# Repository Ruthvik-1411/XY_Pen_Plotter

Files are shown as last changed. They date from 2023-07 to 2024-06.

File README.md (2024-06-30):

# XY_Pen_Plotter
<p align="center">
  
</p>
<p>The pen plotter is a drawing machine capable of creating complex designs, patterns, and artworks on paper or flat surfaces. It a type of CNC (Computer Numerical Control) machine designed to draw or sketch images using a pen or similar writing instrument. It operates on two or more axes, allowing precise control over the movement of the pen across the drawing surface. The pen plotter can execute complex patterns and designs with exceptional accuracy, making it an excellent tool for both artistic and technical applications.This repository contains all the information and resources you need to build your very own pen plotter.</p>

### Key Features
* <b>Low cost:</b> The structure of the pen plotter is made mostly out of wooden blocks and connected using available screws. The base for linear movement is achieved using linear rods that are extracted from a mini drafter. The electronic part of the plotter also uses 28byj-48 steppers which are the cheapest steppers. Most of the components of the plotter are just things lying around in the house.
* <b>Single Stepper Motor for X-Axis Movement:</b> The X-axis movement is managed by a 28byj-48 unipolar stepper motor, providing precise control over the horizontal positioning of the pen.
* <b>Two Stepper Motors for Y-Axis Movement:</b> The pen plotter features two stepper motors that work in parallel to control the movement of the pen along the Y-axis. This enables smooth and synchronized motion for creating detailed drawings.
* <b>GT2 Timing Belts for Enhanced Performance:</b> The plotter uses GT2 timing belts, known for their reliability and reduced backlash, ensuring consistent and accurate drawings.
* <b>Customizable Software Control:</b> The pen plotter is compatible with popular CNC software like GRBL (G-code sender) and can be easily controlled through a computer interface.

## Tools and Materials
* Wooden blocks (54x7 - 2, 40x7 - 2) any size to make a |=| structure.
* Smooth linear rods (from mini drafter) - 6 (2 along x, 4 along y in parallel)
* Rollers or linear bearings that allow for linear motion on rods.
* screws and other misc components for mechanical support
* 28byj-48 uniploar steppers - 3
* ULN2003 stepper motor driver - 3
* GT2 timing belt 1 mtr - 3
* 16 teeth 5mm bore timing pulley - 6(3 at motor shaft, 3 at other end)
* SG90 servo motor
* Limit switches - 3
* Arduino Uno R3 and jumper wires
* Capacitor 100nF (104) - 2
* Resistor 4.7K&#8486; (4k7) - 2
* Prototype board or breadboard
* USB cable and adapter (5V, ~1A) 
* Drilling tool would be handy
* Marker or pen and paper

## Hardware specifications and assembly
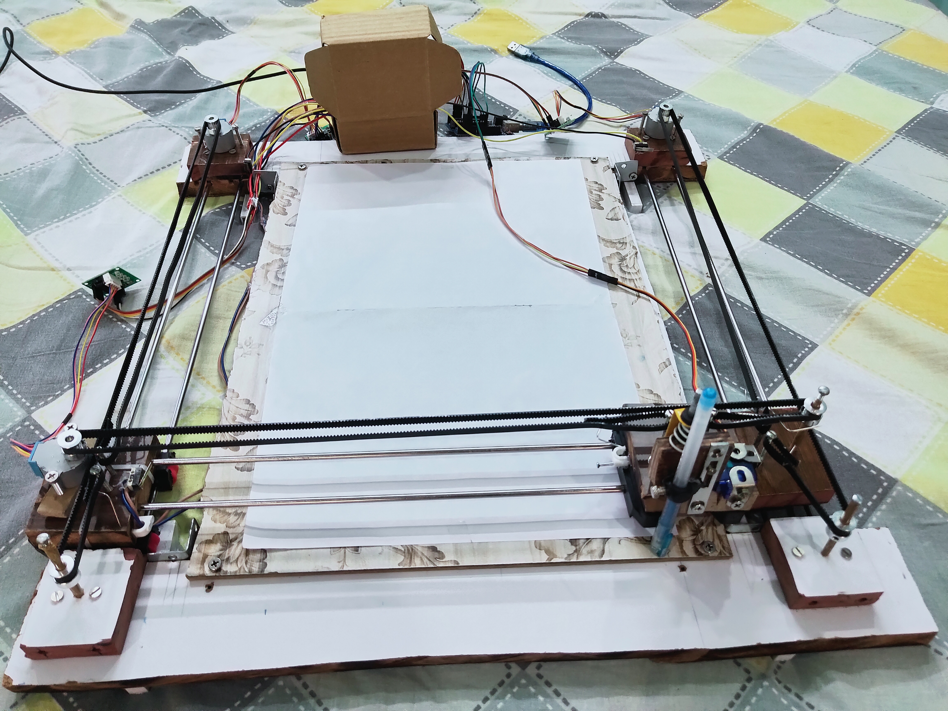
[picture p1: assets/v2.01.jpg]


* <b>The Structure:</b> The wooden blocks can be made into any dimension but it should have 4 units. Two units between which the vertical rods are fixed at each end. To maintain the structure and a constant distance between the units, two smaller blocks are attached. If not they become a parallelogram shape. By adding intermediate blocks it gives a rectangular shape with fixed shape. It is as shown in the figure above.
* <b>The Carriers:</b> To move on the linear rods along x,y direction three blocks are placed. Two pairs of linear rods run on each side parallely (y-axis) as seen in the figures above. Two wooden blocks are placed on each side(on the rods) and between these two parallel blocks runs the third pair of linear rods responsible for x motion. On these rods for x axis lies the third block which has the pen lifting mechanism.
* <b>Stable linear motion:</b> The linear motion can be achieved by using linear bearings or similar kind of structure. Initially I tried using wheels similar to the way train runs on tracks. One challenge of this is the wheels have a small point of contact and they tend to bend toward the motion. The situtation can be better understood by considering a cycle is moving on a linear rod, when an incredible force is applied on one end say back tire, the front tire will rise up. Since the blocks sit on top of these small wheels when they are pulled to one side, the other edge rises up. When the wooden block on the y-axis bend towards one side the entire x-axis blocks which lie on top of this also bend in that direction. This bends the pen lifter and produces bad results. So I used bearings which are around the linear rod rather than wheels that only stay on top of the rods. When they are around the rod the blocks are bound to the rod. Unlike before there will be no motion upwards or downwards.
* <b>Motors and belts:</b> Since there are two motors for y axis movement, they are fixed on one end. The third motor responsible for x motion stays on one of the moving blocks placed on y axis rods. The 5mm pulley is tightened to the shaft of each motor and a pulley is kept on the other end around a linear rod. The GT2 timing belt runs between the shaft of motor and freely moving pulley on the other end. The two ends of the timing belt are fixed around two screws on the moving blocks as shown in the below images.
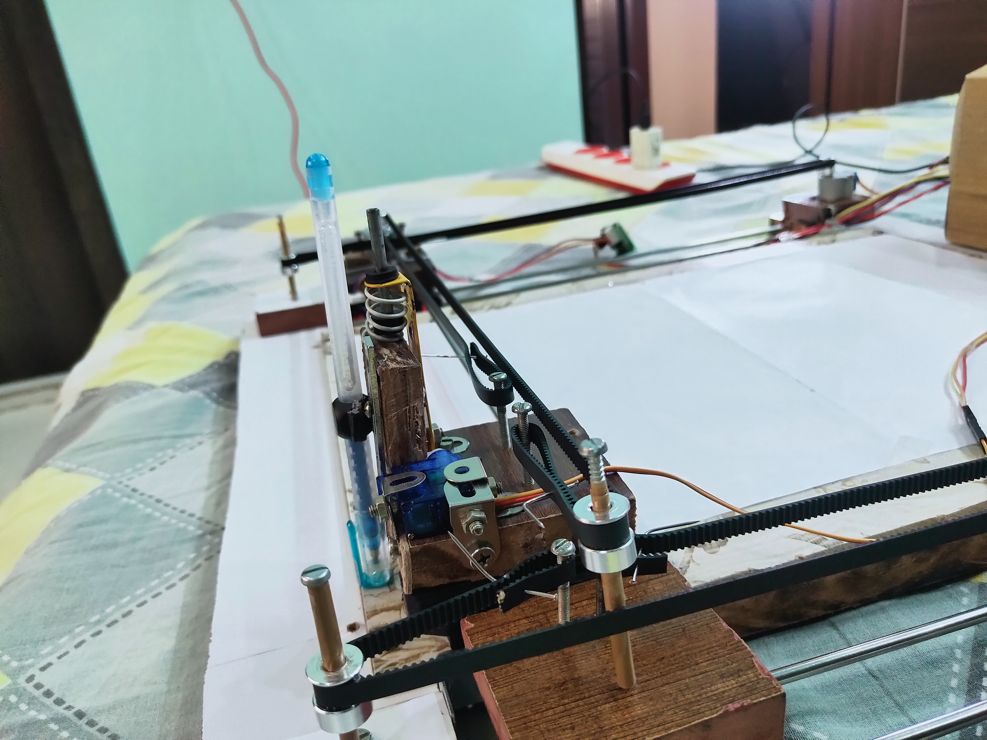
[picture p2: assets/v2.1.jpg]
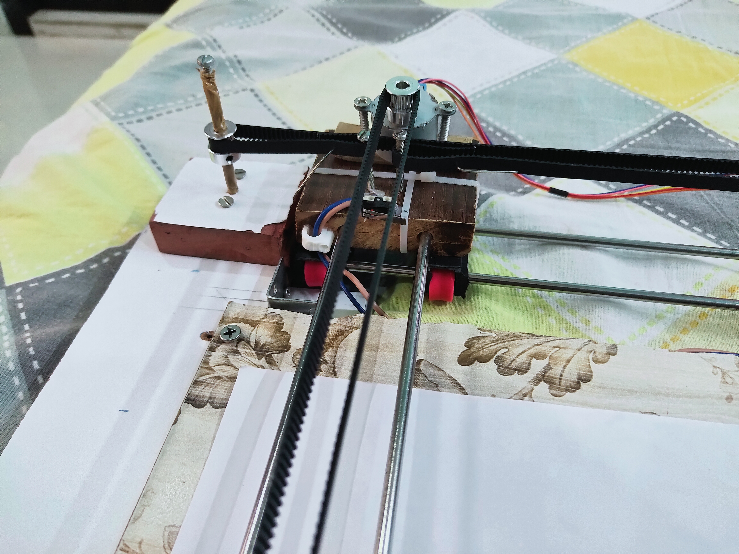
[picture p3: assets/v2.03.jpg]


* <b>The pen lifter:</b> A simple pen lifter is made using some mechanix I had with me. When servo moves a certain angle i.e. when the shaft of the servo rises it lifts the pen holder and keeps it there. When returned to zero the spring pushes the pen holder downwards. The pen holder and <b>pen lifting mechanism was one of the most complex part of the plotter</b>. Many pen holders and pen lifting mechanisms are available online, but they are quite expensive, so a simple mechanism was developed. I could not add a detailed picture of this mechanism as all the parts are fixed and removing them will make it difficult to mount again. But by watching the demo video and images you can get an idea of how it works and the mechanism.
* <b>Limit switch:</b> The motion is made possible along x,y directions and even the pen lifting mechanism is established and the plotter can move around in any direction it wants and actuate the pen accordingly. But one important aspect of the plotter is that it has a restricted space for movement. It should move only between the motor and its opposite end. The software can give instructions to the motors to move around, but it is not aware of the <b>limits</b> of motion. For the system to understand the physical limits of the world limit switches are added at the physical ends of the plotter. 
  * There are two approaches to add the limit switch, one is the home position approach where limit switches are placed at the starting position of the block. The user can then give soft limits i.e the maximum distance the plotter can travel in a given direction. If the other end is 300mm far away then 300 will be the soft limit in that direction. The software stops the motor after it moves that distance away from the start.
  * The other is end of travel approach, where limit switches are placed on the other end of the motor and when the block hits the switch, the software understands that it has hit the physical end on the other side and stop. Without the limit switch the blocks will either ram straight into the motor or worse, damage the belt after getting stuck on other end.
* <b>Connections and wiring:</b> The plotter can now truly travel in the xy space <b>safely</b>. The wiring of the switches and motors can be done by connecting the motor to the driver and powering the pins. In this setup the block's home position is the far end, opposite of the motor and the motor rotates in the direction such that the blocks move towards the motor. This makes the wiring easy as limit switches are placed near motor. The control pins are connected according to the direction of motion that is required. By reversing the control pins the direction can be reversed. In this setup, the y axis steppers should move in opposite directions for the plotter to move in one direction i.e. the belt is fixed in such a way. Both the y axis steppers should actuate same time, so the control pins are combined and a single set of pins is powered. The circuit for the setup is as shown below.
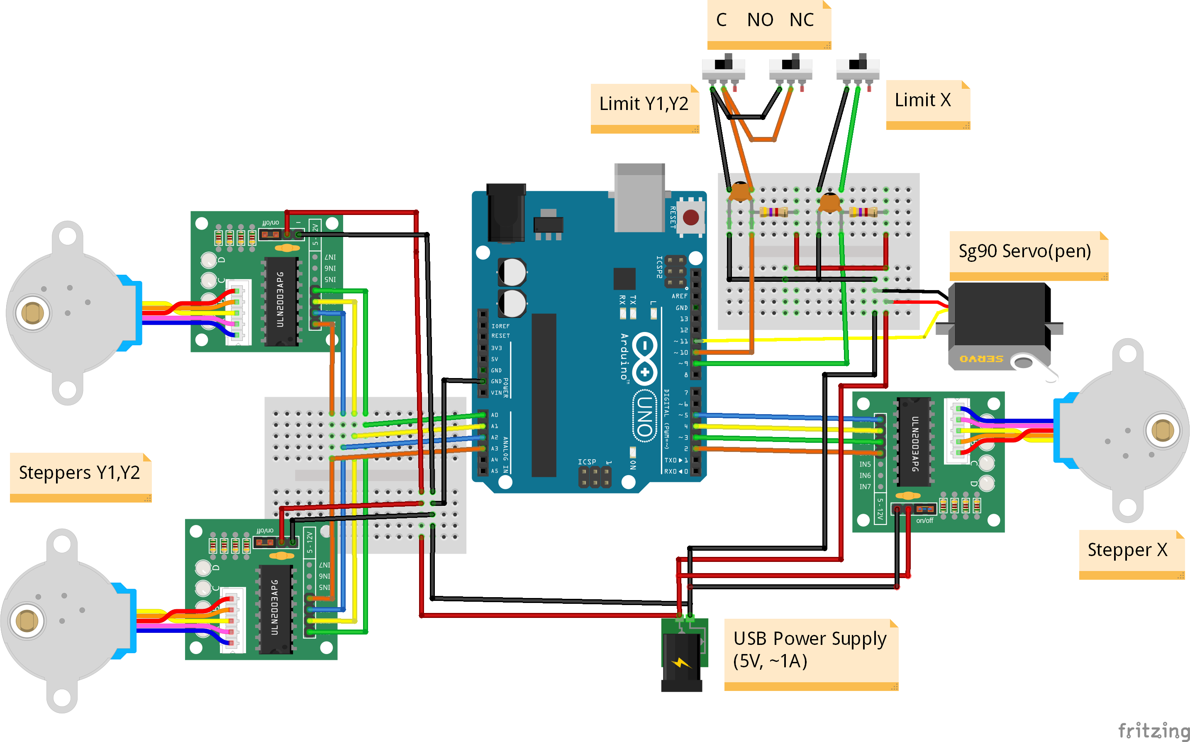
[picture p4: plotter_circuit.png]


## Software specifications and setup
* <b>The complexity:</b> All that is left for the system to do is to control the motors(their direction, speed), monitor the limit switches and actuate the servo that handles the pen lifting. The obvious approach is to use a microcontroller to take care of these things. Arduino is the first thing that comes to mind. Code can be written to monitor the limit switches and by following some examples you can run the steppers as well. The code to do the action as simple as drawing a rectangle becomes quite large. This is because the stepper is controlled by moving a certain number of steps. This rotates the shaft by certain angle and thus the gt2 belt traverses some distance. A correlation between number of steps and distance (in real world) should be calibrated and added into the code. The code should run the motors for some duration, make changes and so on. This makes the code very complex and large. That's where gcode is used.
* <b>The solution:</b> G-code (Geometric code) is a programming language for cnc machines. It is used to tell the machine what to do and how to do by using certain commands and dividing complex shapes and works into smaller tasks. Gcode commands looks like this G## X## Y## F##.
    * G## - for specific action, move in straight line(linear interpolation), circular interpolation clockwise etc
    * X##,Y## - set the end position
    * F## - feed rate(speed of action)
* <b>Making gcode:</b> The machine performs these actions based on a G code. Where do we get the Gcode from? Well, first let's say you want to draw something, say your name or an image. There is something called <a href="https://inkscape.org/">inkscape</a>. It is like MS paint but better suited for cnc purposes. An image or text can be drawn in the inkscape. Now for a cnc machine or an xy plotter everything you draw or write is finally a path that the actuator has to move along. Inkscape can convert the drawing into a path as a combination of linear,clock, anti clock wise and other movements. You can select the drawing and convert into path by choosing path->object to path option. This path that the inkscape generated should be converted to g code. It should also add in the factor of the pen lifting. The setup of inkscape looks like below.
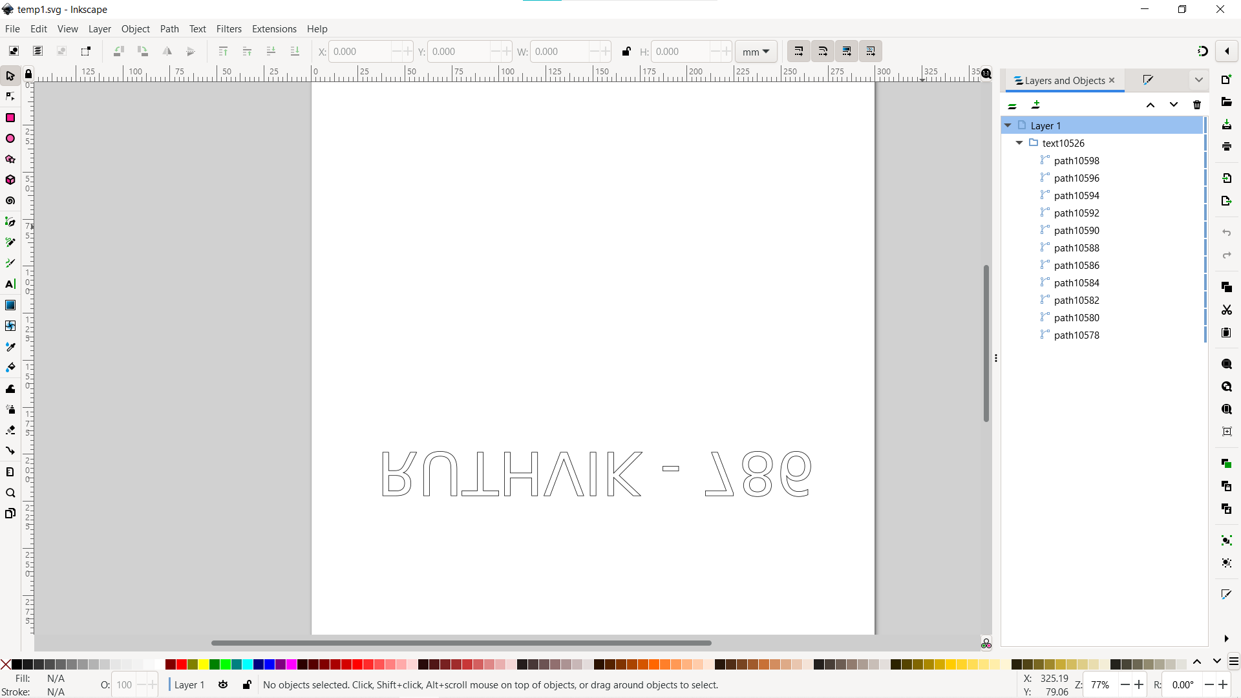
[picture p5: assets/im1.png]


* <b>The helper:</b> <a href="https://github.com/arpruss/gcodeplot/releases">G code plot</a> is an inkscape extension which can do this for us. Dowload the zip file from here and extract it. To add this extension you should copy the contents of the gcodeplot folder and paste it at "C:\Program Files\Inkspace\share\inkscape\extensions". The location can vary but this should be in the main Inkscape folder. Now open the inkscape, create the drawing, convert the object to path and choose save as ".gcode". The gcode plot now asks for some options which can be configured accordingly, but best left the same. The importance of gcodeplot doesn't lie on converting into gcode but allowing the user to add a servo lift action. When you click save as .gcode, a gcodeplot window pops up. In the cutting setting you can add the pwm signal that the servo requires for lifting. Lift up and Lift down commands can be given. M05 means "zero deg" and M03 xxx(0-255) corresponding to 0-180 deg rev. Since the gcode should also include the lift commands these commands are placed wherever required.
  * One thing that should change is that the drawing that was first made should be made upside down. This is because the inkscape origin is at top left. But gcodeplot's origin is at bottom left. By inverting the drawing upside down, the machine can draw it exactly as required or else the result will be an upside down copy. The process is same for other steps.
*  <b>GRBL:</b> We can now convert our drawings into gcode. How can we tell the motors or our controller to perform actions based on this? That's where <a href="https://github.com/grbl/grbl">GRBL</a> comes in. GRBL is an open source software or firmware which enables motion control for CNC machines. We can easily install the GRBL firmware to an Arduino and so we instantly get a low cost, high performance CNC controller. The GRBL uses G-code as input, and outputs motion control via the Arduino. GRBL is the interpretor that converts the gcode into the motor control and monitoring limit switches. GRBL is designed for arduino boards. There are specific pins that the motors, switches should be connected to. But the official GRBL is designed for bipolar stepper motors with cnc controllers and driver boards. The setup that is made uses unipolar 28byj-48 stepper motors and also has servo motor. Official <a href="https://github.com/grbl/grbl">GRBL</a> isn't developed for this setup. We have to improvise and look for a firmware that suits our setup.
*  <b>The solution:</b> Thankfully someone has painfully gone through all the code in the official grbl and made changes that fit our setup. The repository made by ruizivo <a href="https://github.com/ruizivo/GRBL-28byj-48-Servo">https://github.com/ruizivo/GRBL-28byj-48-Servo</a> can be used for this setup. It is like a library that can be added to arduino and uploaded as a sketch into arduino uno. The zip file can be downloaded and the grbl folder can be copied into the the libraries of arduino software. The grbl folder has some c and header files. Some files need to be changed for the software to work. The <a href="https://github.com/Ruthvik-1411/XY_Pen_Plotter/tree/main/grbl"> grbl</a> folder that is available in this repo has all the changes that are needed for the setup to work. It can be pasted into the library folder of arduino software and it's done. Just download the grbl folder from above and paste it in libraries.
*  <b>GRBL with arduino:</b> The GRBL firware that is suited for this setup can be uploaded into the arduino by going to examples, scrolling down and choosing grblUpload file. The file is also available in this repo. Now the arduino can interpret the gcode that it receives. Now we have the gcode and an arduino microcontroller that can understand the gcode and actuate the stepper motors,servo motor and monitor the limit switches. But how can we send the gcode to arduino? We have <a href="https://winder.github.io/ugs_website/download/">UGS</a> (Universal Gcode Sender), an open source and widely used software compatible with many cnc machines that are available. UGS takes gcode as an input and sends tha gcode to arduino controller at specific baud rate. GRBL uses a standard 115200 buad rate to communicate with arduino. But UGS has to be configured for each machine. Once configured it can work with any drawing and task at hand.
*  <b>The manager UGS:</b> UGS requires the grbl to be installed on the controller beforehand. Now you can connect the arduino and connect to the arduino from ugs. You can follow the setup wizard that's built-in ugs or manually change the settings. Some major configuration that are required are :
    *  Setup Wizard:
        * After connecting the controller and making the connections with motors and switches accordingly, you can proceed with the wizard. You can check the direction of rotation of motor and change the software postive direction or physically reverse the control pins.
        * Now the software should be calibrated according to the movement made in physical world. Stepper motors move in steps and software has control over number of steps to rotate, but it should be related to the distance to be moved. So steps/mm should be calibrated. Initially 250 steps is considered as 1mm in software. Grbl moves 250 steps and respective distance travelled by the blocks should be taken to calibrate the software. The estimate is given so that 1mm in software will equal 1mm in physical world. The value of estimated steps/mm allows the software to control 1mm distance in real world by moving the specific number of steps.
        * Limit switches can be checked by manually triggering them and buttons change in colour or create an alarm. The switches action can also be inverted depending on the circuit.
        * Homing option can be enabled to let the system check its working. It can be skipped if there is any error in software.
   * Manual Commands:
        *  When arduino is connected there are a set of commands displayed with $ sign infront of them. Each command has their own significance. For more information you can check this <a href="https://honingmill.fandom.com/wiki/Configuring_Grbl_v0.9">wiki</a>. Some commands that should be changed are $5,20,21,24,25,100,101,110,111,130,131.
        *  $5 - to invert limit switch(1),$20 - to activate soft limits(max travel)(1),$21 - to activate hard limit(1),$24 - to set homing speed(speed,if homing is active),$25 - to set homing seek speed,$100,101 - the steps/mm calibrated previously for x,y,$110,111 - the maximum speed of x,y steppers,$130,131 - max travel from end to end of x,y axis in mm. The changes can be made by entering $x=value and hitting enter. These change happen when setup wizard is used as well.
     *  After configuring the GRBL parameters for the setup, all you have to do is send the gcode to arduino and the software takes care of the rest.
* <b>Software setup:</b> Now that arduino can understand what to do and how to do it, all it needs is the gcode from ugs. The gcode that is complied from gcode plotter can be loaded into the ugs and the drawing can be seen in the visualizer. The setup looks like below.
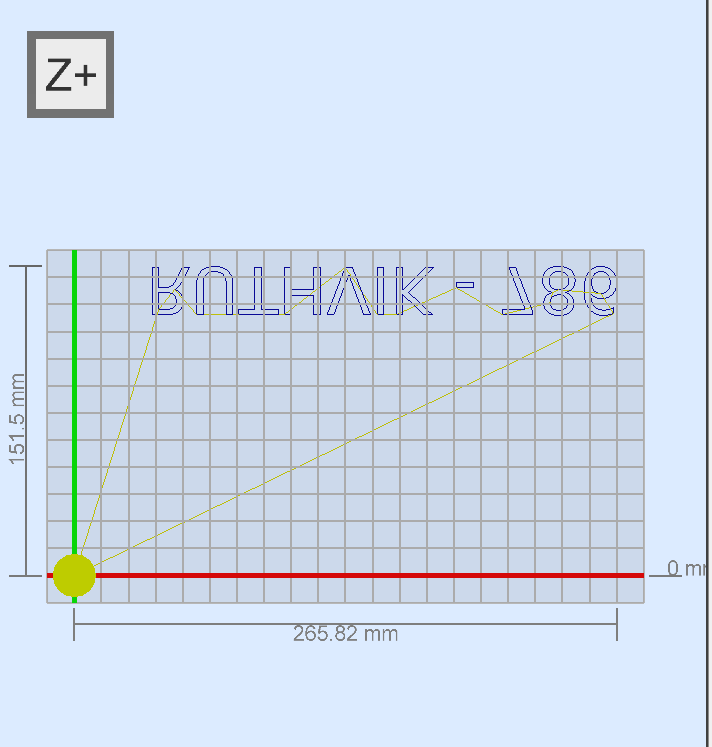
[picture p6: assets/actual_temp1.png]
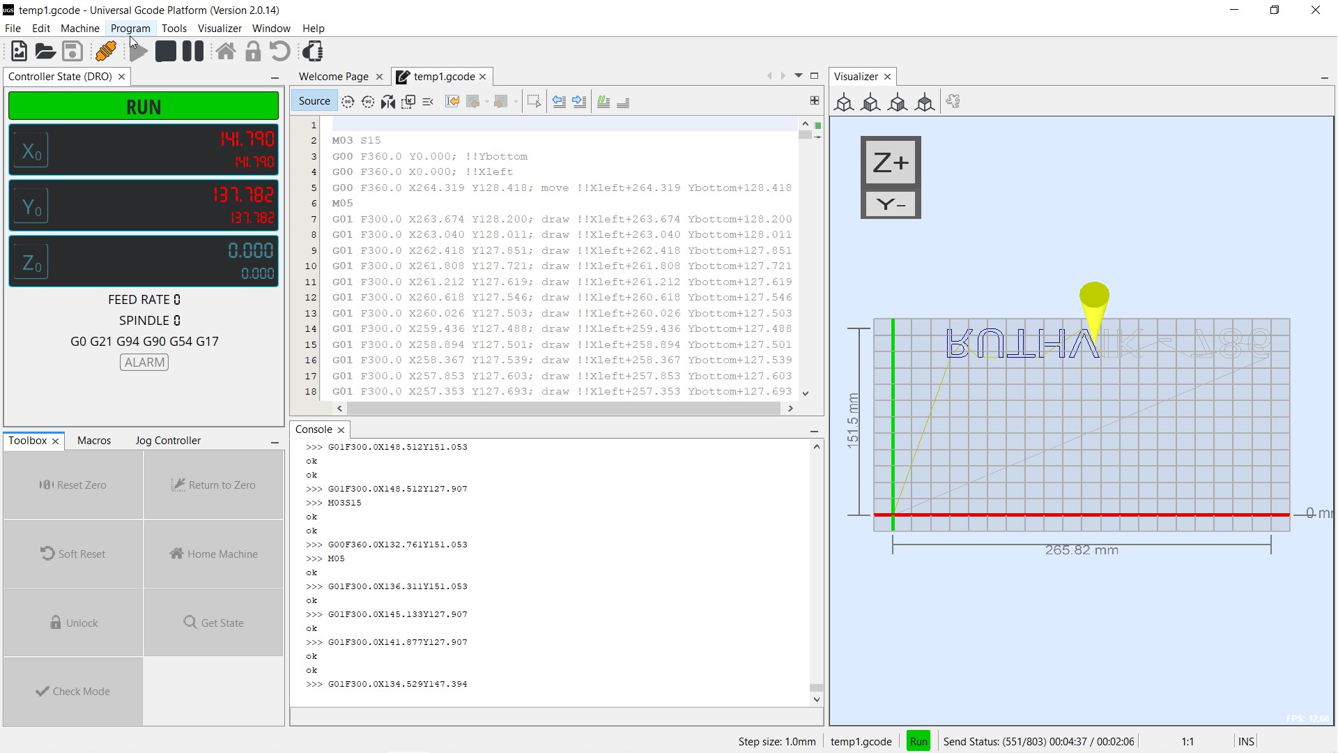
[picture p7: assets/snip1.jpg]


* <b>To avoid errors:</b> Now, there is one change that needs to be made in the gcode file. While GRBL and the gcode plotter are built to accommodate a z-axis, the current setup does not have such a feature. To avoid any potential errors, it is necessary to remove all commands before the first pen lift command, which occurs approximately 10 lines into the code. The gcode starts with a pen lift command, and upon completing the drawing, the plotter lifts the pen. However, the gcode leaves the plotter in its last position, whereas we want it to return to the home position after completing the drawing. To achieve this, after the last pen lift command, simply add the line "G00 F350.0 X0.00 Y0.00".

*  The plotter setup is now complete and any drawing can be converted to gcode as seen above. The gcode can be edited a little and it can be sent to the arduino. The working of the plotter can be seen in the <a href="https://youtu.be/HnFqBWPk73Q">demo video</a> below. The gallery with all the images can be found here <a href="Gallery.md">Gallery.md</a>.
<table align="center">
  <tr>
    <td>
      <a href="http://www.youtube.com/watch?v=HnFqBWPk73Q" target="_blank">
        Pen Plotter from trash
      </a>
    </td>
    <td>
      <a href="http://www.youtube.com/watch?v=aX3epN6Ej_w" target="_blank">
        UGS Setup
      </a>
    </td>
  </tr>
</table>

## Improvements
* The rollers used in this plotter are homemade, and some adjustments have been made to optimize their performance. However, incorporating linear bearings along with the rods can yield more ideal results, providing smoother and more precise movement.
* GT2 timing belts are commonly employed in various CNC machines. In this particular setup, the belt is wound tightly around the ends. However, due to the combination of a long distance and a relatively weak structure (the steppers fixed with only two screws, and the belt ends fixed between screws), some sagging occurs despite the tight winding. Tightening the belt further compromises the structure, leading to a trade-off. When the motor rotates, the belt experiences sufficient tension initially, but it loses the sag before moving, causing a delay in movement and resulting in inaccurate drawings.
## External Links
* Inkscape - [https://inkscape.org/](https://inkscape.org/)
* Gcode Plot extension - [https://github.com/arpruss/gcodeplot/releases](https://github.com/arpruss/gcodeplot/releases)
* GRBL official repo - [https://github.com/grbl/grbl](https://github.com/grbl/grbl)
* GRBL 28byj-48 + servo repository - [https://github.com/ruizivo/GRBL-28byj-48-Servo](https://github.com/ruizivo/GRBL-28byj-48-Servo)
* Edited GRBL folder - [https://github.com/Ruthvik-1411/XY_Pen_Plotter/tree/main/grbl](https://github.com/Ruthvik-1411/XY_Pen_Plotter/tree/main/grbl)
* UGS - [https://winder.github.io/ugs_website/download/](https://winder.github.io/ugs_website/download/)
* CNC commands - [https://honingmill.fandom.com/wiki/Configuring_Grbl_v0.9](https://honingmill.fandom.com/wiki/Configuring_Grbl_v0.9)
* Thanks to chronic mechatronic for the awesome tutorial for software issues - [https://youtu.be/f6xCfzfiD6Q](https://youtu.be/f6xCfzfiD6Q)
* Demo Video - [http://www.youtube.com/watch?v=HnFqBWPk73Q](http://www.youtube.com/watch?v=HnFqBWPk73Q)
* UGS Demo Video - [https://youtu.be/aX3epN6Ej_w](https://youtu.be/aX3epN6Ej_w)

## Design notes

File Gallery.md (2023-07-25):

# Project Gallery
Some images of the xy pen plotter are displayed here.
### Version 1.0 - Wheeled base


### Version 2.0 - circular base
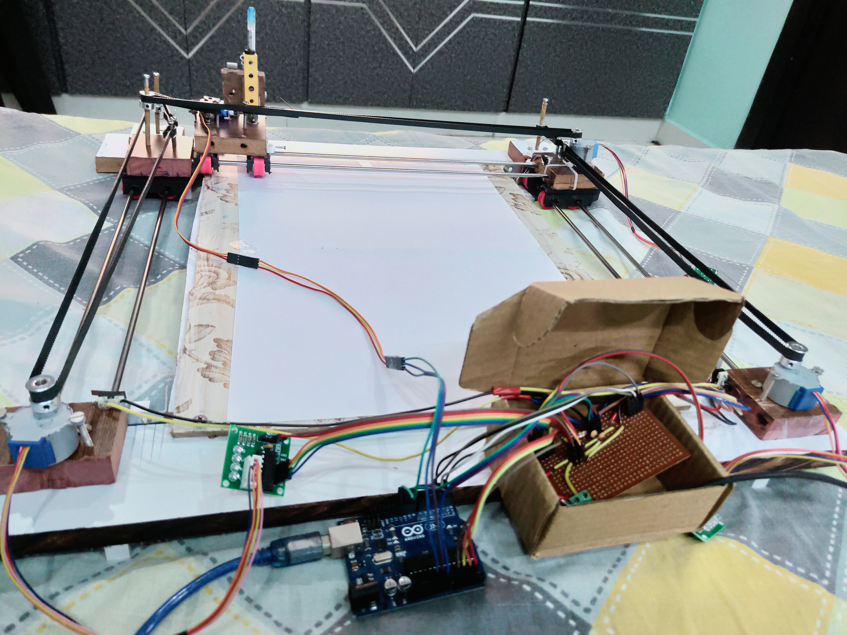
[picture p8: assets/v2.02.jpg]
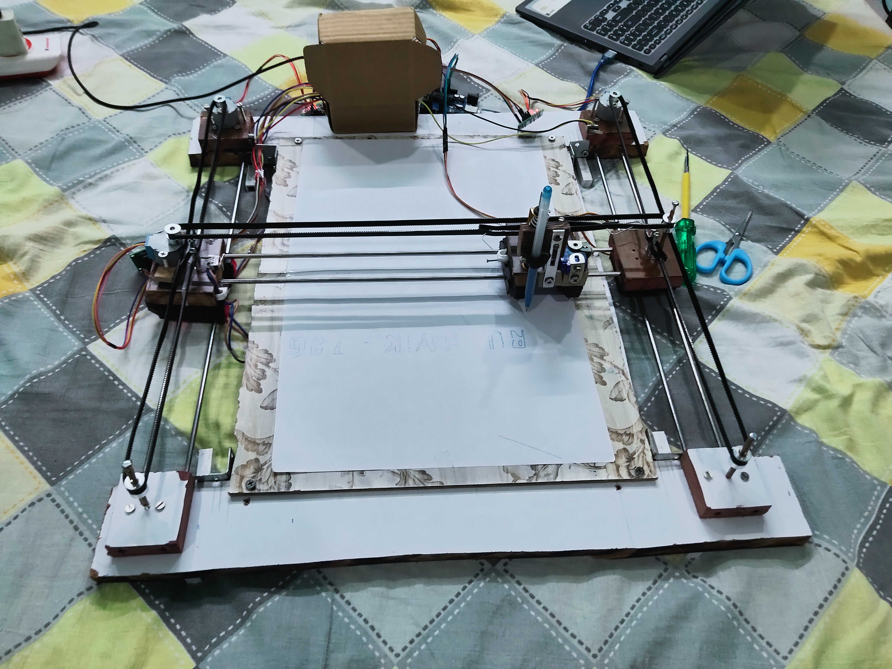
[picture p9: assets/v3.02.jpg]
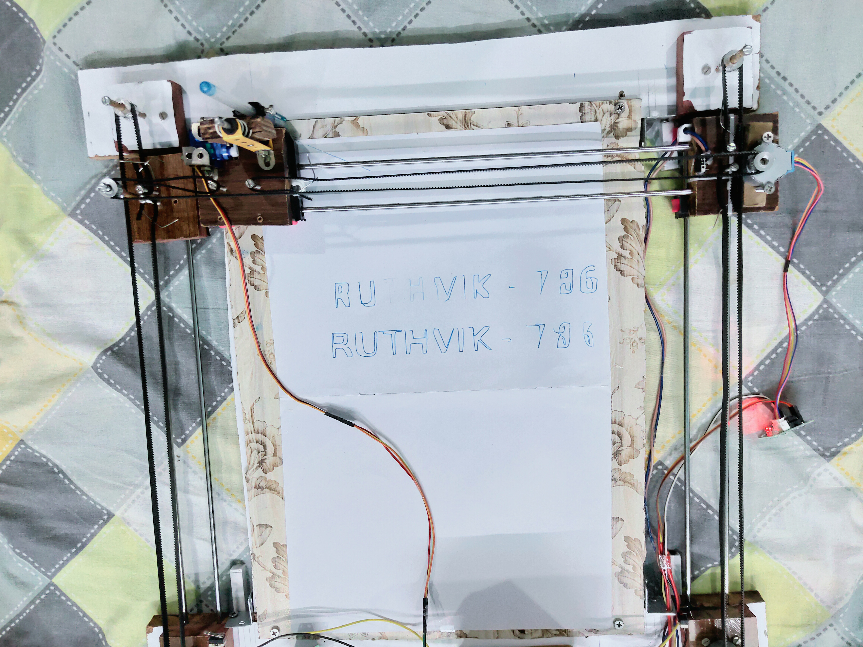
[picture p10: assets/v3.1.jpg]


### Software


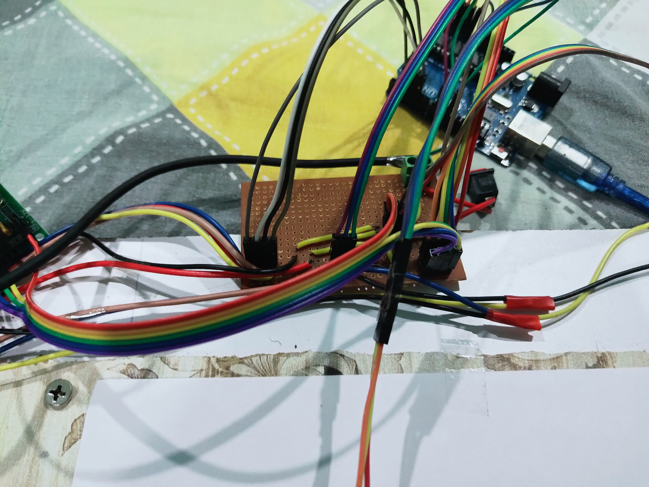
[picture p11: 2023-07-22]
assets/v1.1.jpg

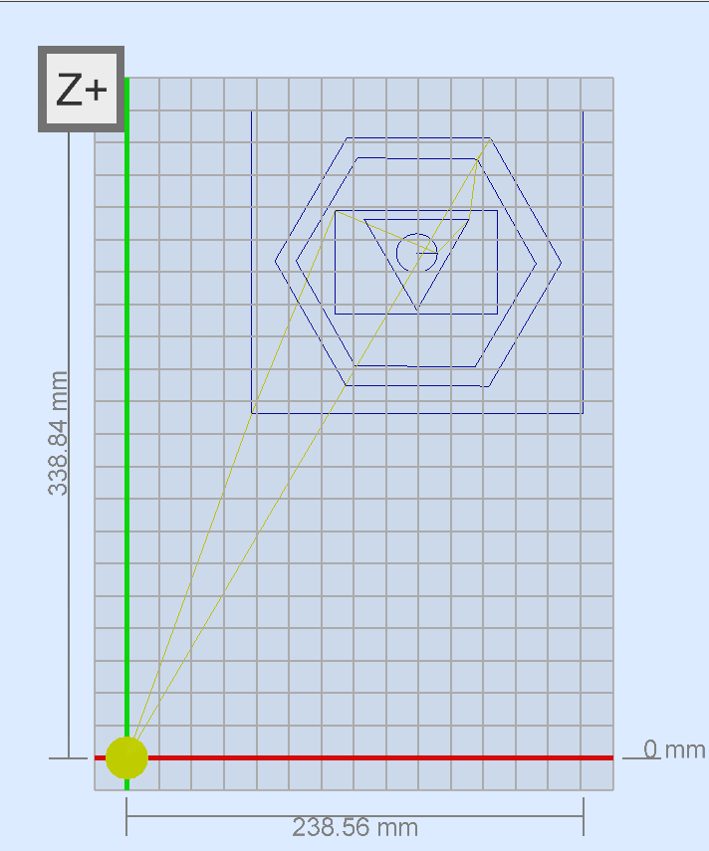
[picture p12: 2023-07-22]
assets/actual_img1.png

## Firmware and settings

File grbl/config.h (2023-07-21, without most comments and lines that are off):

#define config_h
#include "grbl.h" // For Arduino IDE compatibility.
#define DEFAULTS_GENERIC
#define BAUD_RATE 115200
#define CPU_MAP_ATMEGA328P // Arduino Uno CPU
#define CMD_STATUS_REPORT '?'
#define CMD_FEED_HOLD '!'
#define CMD_CYCLE_START '~'
#define CMD_RESET 0x18 // ctrl-x.
#define CMD_SAFETY_DOOR '@'
#define HOMING_INIT_LOCK // Comment to disable
#define HOMING_CYCLE_0 (1<<X_AXIS)
#define HOMING_CYCLE_1 (1<<Y_AXIS)
#define N_HOMING_LOCATE_CYCLE 1 // Integer (1-128)
#define N_STARTUP_LINE 2 // Integer (1-2)
#define N_DECIMAL_COORDVALUE_INCH 4 // Coordinate or position value in inches
#define N_DECIMAL_COORDVALUE_MM   3 // Coordinate or position value in mm
#define N_DECIMAL_RATEVALUE_INCH  1 // Rate or velocity value in in/min
#define N_DECIMAL_RATEVALUE_MM    0 // Rate or velocity value in mm/min
#define N_DECIMAL_SETTINGVALUE    3 // Decimals for floating point setting values
#define MESSAGE_PROBE_COORDINATES // Enabled by default. Comment to disable.
#define SAFETY_DOOR_SPINDLE_DELAY 4000
#define SAFETY_DOOR_COOLANT_DELAY 1000
#define ACCELERATION_TICKS_PER_SECOND 100
#define ADAPTIVE_MULTI_AXIS_STEP_SMOOTHING  // Default enabled. Comment to disable.
#define TOOL_LENGTH_OFFSET_AXIS Z_AXIS // Default z-axis. Valid values are X_AXIS, Y_AXIS, or Z_AXIS.
#define VARIABLE_SPINDLE // Default enabled. Comment to disable.
#define SPINDLE_MAX_RPM 90.0 // Max spindle RPM. This value is equal to 100% duty cycle on the PWM.
#define SPINDLE_MIN_RPM 0.0    // Min spindle RPM. This value is equal to (1/256) duty cycle on the PWM.
#define MINIMUM_JUNCTION_SPEED 0.0 // (mm/min)
#define MINIMUM_FEED_RATE 1.0 // (mm/min)
#define N_ARC_CORRECTION 12 // Integer (1-255)
#define ARC_ANGULAR_TRAVEL_EPSILON 5E-7 // Float (radians)
#define DWELL_TIME_STEP 50 // Integer (1-255) (milliseconds)
#if defined(USE_SPINDLE_DIR_AS_ENABLE_PIN) && !defined(VARIABLE_SPINDLE)
  #error "USE_SPINDLE_DIR_AS_ENABLE_PIN may only be used with VARIABLE_SPINDLE enabled"
#endif
#if defined(USE_SPINDLE_DIR_AS_ENABLE_PIN) && !defined(CPU_MAP_ATMEGA328P)
  #error "USE_SPINDLE_DIR_AS_ENABLE_PIN may only be used with a 328p processor"
#endif

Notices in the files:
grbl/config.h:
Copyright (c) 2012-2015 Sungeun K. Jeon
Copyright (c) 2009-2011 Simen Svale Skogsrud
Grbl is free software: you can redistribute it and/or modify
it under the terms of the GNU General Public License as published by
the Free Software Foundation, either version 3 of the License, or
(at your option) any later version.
